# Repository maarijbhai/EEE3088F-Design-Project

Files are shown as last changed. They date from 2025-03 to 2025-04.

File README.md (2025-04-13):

# Micro Mouse Power Subsystem

This respository contains the datasheets of components used, schematics and production files of a power subsystem of a Micro Mouse. The power subsystem handles the charging, battery monitoring, motor controll and providing power to the various other subsections of a Micro Mouse.

## Table of Contents
- [Overview](#overview)
- [Subsytem Requirements](#subsystem-requirements)
- [File Structure](file-structure)
- [Usage](#usage)
- [Production](#production)
- [Credits](credits)

## Overview

Designed to navigate and solve a maze by itself, the Micro Mouse is a common project with even competitions made to determine who is able to create the fastest and most efficient Micro Mouse. While not on the competition level this project is undertaken by students in the University of Cape Town to put into practice all the theoretical knowledge learnt in their studies. With the hardware and sensoring subsystem designed by the university, the aim of this project is to design the power subsystem that powers the overall design.

## Subsystem Requirements

- Operate up to 4 motors bidirectionally with the pins available to you (listed in the power pinout table). You will need to control 2x brushed DC motors which could each draw 200mA at the highest voltage of a 1S1P battery (the battery is further specified in the battery section). The other 2x motors are for the auxiliary connection and need to operate 500mA each.
- Place an INA219 for monitoring the battery on the I2C Bus and configure it correctly with respect to the hardware (cannot have BOTH A0 AND A1 on GND)
- Charge the battery from the 9V input pin (listed in the power pinout table).
- Have two charging modes for a higher and lower charging current for the battery (200mA, and approximately 600mA ±100mA from the battery perspective.
- Integrate USB C and get 9V out of the USB Host
- Provide 2x External Load Switching at 1A each (High Side connected to your 5V)
- Provide a 3V3 5% accuracy (300mA max) and 5V Out 5% accuracy (1.5A max)
- Provide an ON/OFF switch. OFF state: battery draw <30uA. ON state: can provide your robot peak current of 2A. The switch needs to shut down 5V and 3V3.

## File Structure

Each of the above mentioned requirements are designed seperately under their own folder name ultimately meeting up in the Main project folder. This was to prevent any clashes or errors arising from outdated revisions of the project being worked on. 

The production files (gerbers) can be found inside the Main project folder under "JLCPCB".

## Usage

# Access schematic or PCB:
To view or modify the schematic and/or PCB:
1. Open KiCad 9 or later
2. Load the Main project (or any other desired)
3. Edit or simulate as needed

# To manufacture the PCB:
1. Navigate to the JLCPCB website
2. Upload the Gerber ZIP file
3. Use the provided BOM and CPL files in the JLCPCB file directory inside the main project folder for assembly

## Credits
- Maarij Alam
- Saeed Solomon

Third-party components from Texas Instruments, ON Semiconductor, and others.

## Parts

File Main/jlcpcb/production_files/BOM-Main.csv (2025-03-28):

Comment | Designator | Footprint | LCSC | Quantity
2.2u | C2,C5 | C_0402_1005Metric_Pad0.74x0.62mm_HandSolder | C12530 | 2
0.1u | C14 | C_0603_1608Metric_Pad1.08x0.95mm_HandSolder | C14663 | 1
10u | C18,C4 | C_0402_1005Metric_Pad0.74x0.62mm_HandSolder | C15525 | 2
0.01u | C3,C6 | C_0805_2012Metric_Pad1.18x1.45mm_HandSolder | C1710 | 2
10k | R19,R4 | R_0402_1005Metric_Pad0.72x0.64mm_HandSolder | C17414 | 2
150R | R12 | R_0815_2038Metric_Pad1.20x4.05mm_HandSolder | C17471 | 1
1R | R3 | R_1206_3216Metric_Pad1.30x1.75mm_HandSolder | C17928 | 1
1u | C1,C10,C11,C8 | C_1206_3216Metric_Pad1.33x1.80mm_HandSolder | C1848 | 4
10uF | C17,C19 | C_0402_1005Metric_Pad0.74x0.62mm_HandSolder | C19702 | 2
HUSB237-AA001-DN06R | U3 | DFN-6-1EP_2x2mm_P0.65mm_EP1.01x1.7mm | C22373734 | 1
330k | R20 | R_0603_1608Metric_Pad0.98x0.95mm_HandSolder | C23137 | 1
470k | R22 | R_0603_1608Metric_Pad0.98x0.95mm_HandSolder | C23178 | 1
75k | R1 | R_0603_1608Metric_Pad0.98x0.95mm_HandSolder | C23242 | 1
4.7u | C7,C9 | C_0402_1005Metric | C23733 | 2
R400 | R17,R5,R6 | R_1206_3216Metric_Pad1.30x1.75mm_HandSolder | C247521 | 3
RT9742GGJ5 | U4,U5 | TSOT-23-5_HandSoldering | C250547 | 2
100k | R18,R21 | R_0402_1005Metric_Pad0.72x0.64mm_HandSolder | C25741 | 2
10K | R14,R23 | R_0402_1005Metric_Pad0.72x0.64mm_HandSolder | C25744 | 2
1k5 | R7,R8 | R_0402_1005Metric_Pad0.72x0.64mm_HandSolder | C25867 | 2
2k2 | R11 | R_0402_1005Metric_Pad0.72x0.64mm_HandSolder | C25879 | 1
4k3 | R10 | R_0402_1005Metric_Pad0.72x0.64mm_HandSolder | C25899 | 1
TPS63802DLAR | U7 | VREG_TPS63802DLAR | C2845237 | 1
2k | R9 | R_0402_1005Metric_Pad0.72x0.64mm_HandSolder | C4109 | 1
22u | C12,C13 | C_0402_1005Metric_Pad0.74x0.62mm_HandSolder | C45783 | 2
BQ24074RGT | U1 | VQFN-16-1EP_3x3mm_P0.5mm_EP1.6x1.6mm | C54313 | 1
AMS1117-3.3 | U9 | SOT-223-3_TabPin2 | C6186 | 1
TYPE-C 6P | J2 | USB_C_Receptacle_GCT_USB4125-xx-x_6P_TopMnt_Horizontal | C668623 | 1
S9013 J3(RANGE:200-350) | Q3 | SOT-23_Handsoldering | C6749 | 1
INA219AxDCN | U6 | SOT-23-8_Handsoldering | C87469 | 1
47u | C15,C16 | C_0402_1005Metric_Pad0.74x0.62mm_HandSolder | C96123 | 2
DRV8833PW | U2 | TSSOP-16_4.4x5mm_P0.65mm |  | 1
TestPoint | TP18 | TestPoint_Pad_D1.0mm |  | 1
TestPoint | TP11 | TestPoint_Pad_D1.0mm |  | 1
TestPoint | TP4 | TestPoint_Pad_D1.0mm |  | 1
DRV8833PW | U8 | TSSOP-16_4.4x5mm_P0.65mm |  | 1
1k | R13 | R_0402_1005Metric_Pad0.72x0.64mm_HandSolder |  | 1
TestPoint | TP14 | TestPoint_Pad_D1.0mm |  | 1
TestPoint | TP13 | TestPoint_Pad_D1.0mm |  | 1
TestPoint | TP2 | TestPoint_Pad_D1.0mm |  | 1
KT-0603R | D1 | LED_KT-0603R |  | 1
TestPoint | TP6 | TestPoint_Pad_D1.0mm |  | 1
TestPoint | TP15 | TestPoint_Pad_D1.0mm |  | 1
TestPoint | TP9 | TestPoint_Pad_D1.0mm |  | 1
TestPoint | TP12 | TestPoint_Pad_D1.0mm |  | 1
TestPoint | TP16 | TestPoint_Pad_D1.0mm |  | 1
TestPoint | TP8 | TestPoint_Pad_D1.0mm |  | 1
KT-0603R | D2 | LED_KT-0603R |  | 1
TestPoint | TP17 | TestPoint_Pad_D1.0mm |  | 1
TestPoint | TP3 | TestPoint_Pad_D1.0mm |  | 1
TestPoint | TP19 | TestPoint_Pad_D1.0mm |  | 1
TestPoint | TP5 | TestPoint_Pad_D1.0mm |  | 1
TestPoint | TP10 | TestPoint_Pad_D1.0mm |  | 1
SS-12D11G3R | SW2 | SW-TH_SS-12D11L3 |  | 1
TestPoint | TP1 | TestPoint_Pad_D1.0mm |  | 1
470nH | L1 | L_0603_1608Metric_Pad1.05x0.95mm_HandSolder |  | 1
TestPoint | TP7 | TestPoint_Pad_D1.0mm |  | 1
TestPoint | TP20 | TestPoint_Pad_D1.0mm |  | 1

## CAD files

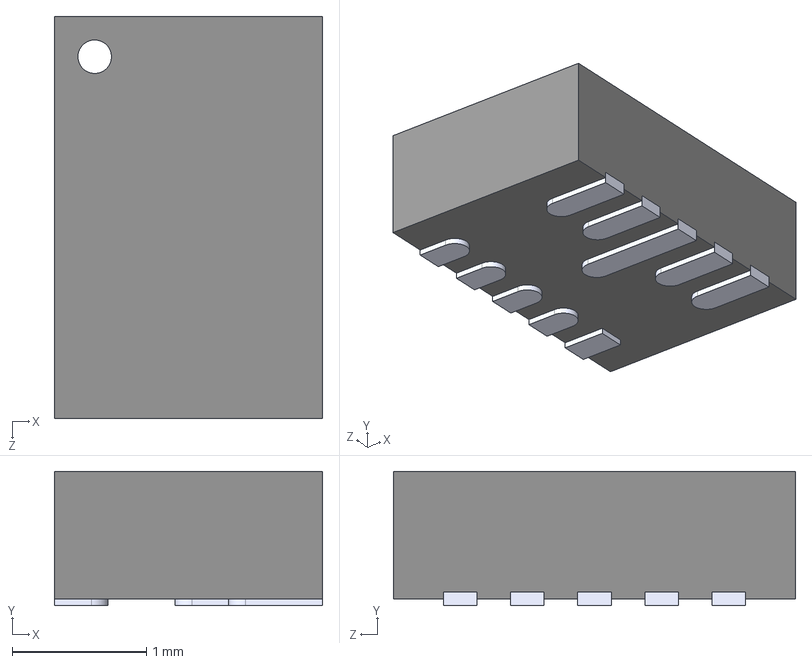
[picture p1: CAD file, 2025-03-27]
Component Footprints/TPS63802DLAR/TPS63802DLAR.step
2.00 x 1.00 x 3.00 mm

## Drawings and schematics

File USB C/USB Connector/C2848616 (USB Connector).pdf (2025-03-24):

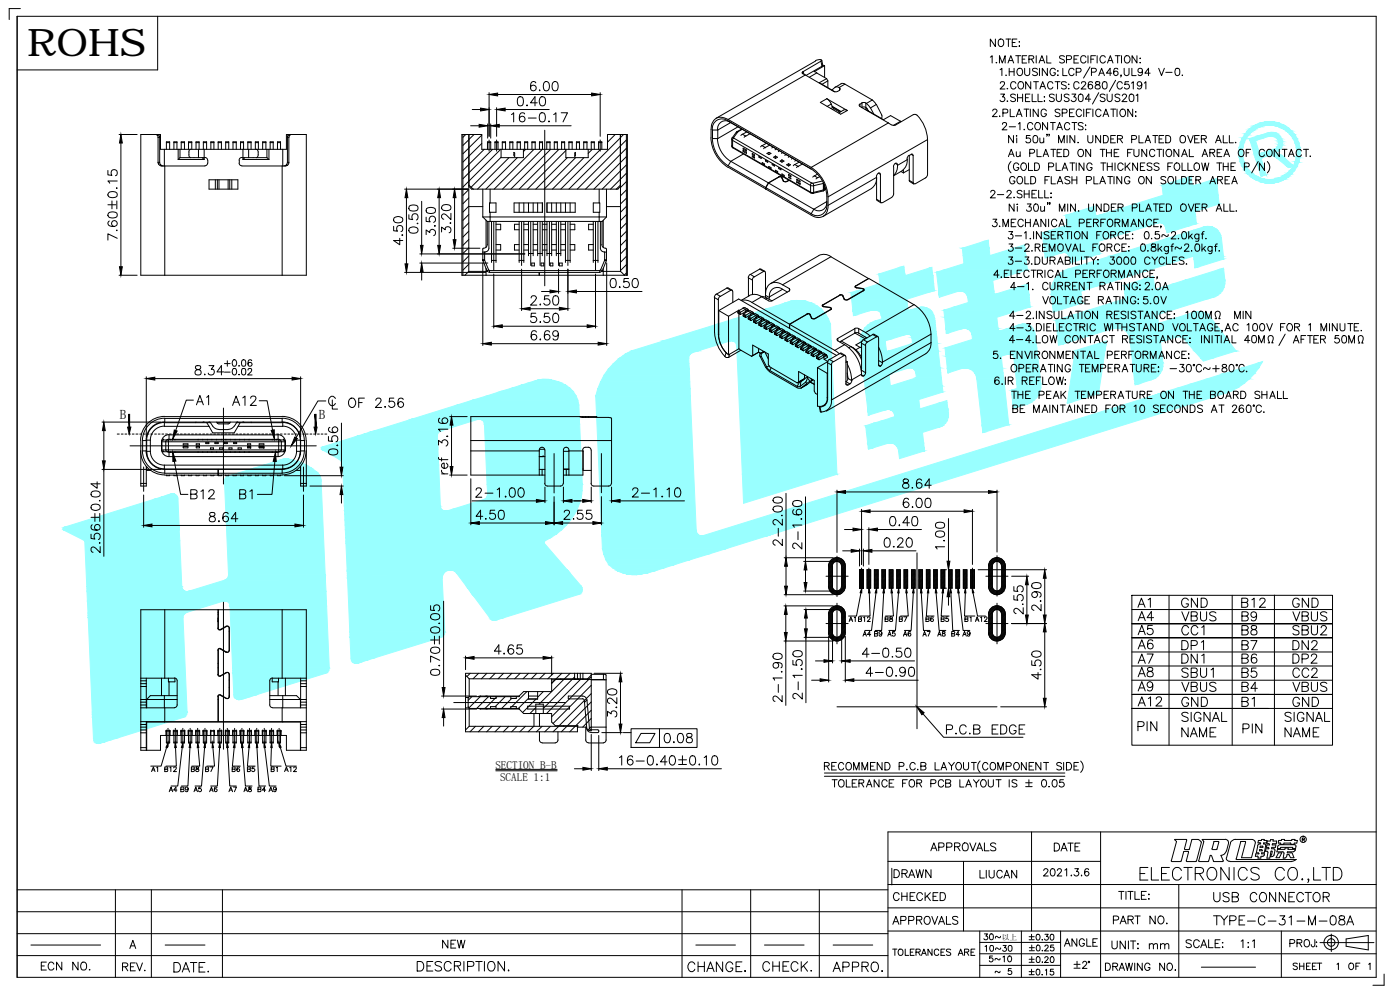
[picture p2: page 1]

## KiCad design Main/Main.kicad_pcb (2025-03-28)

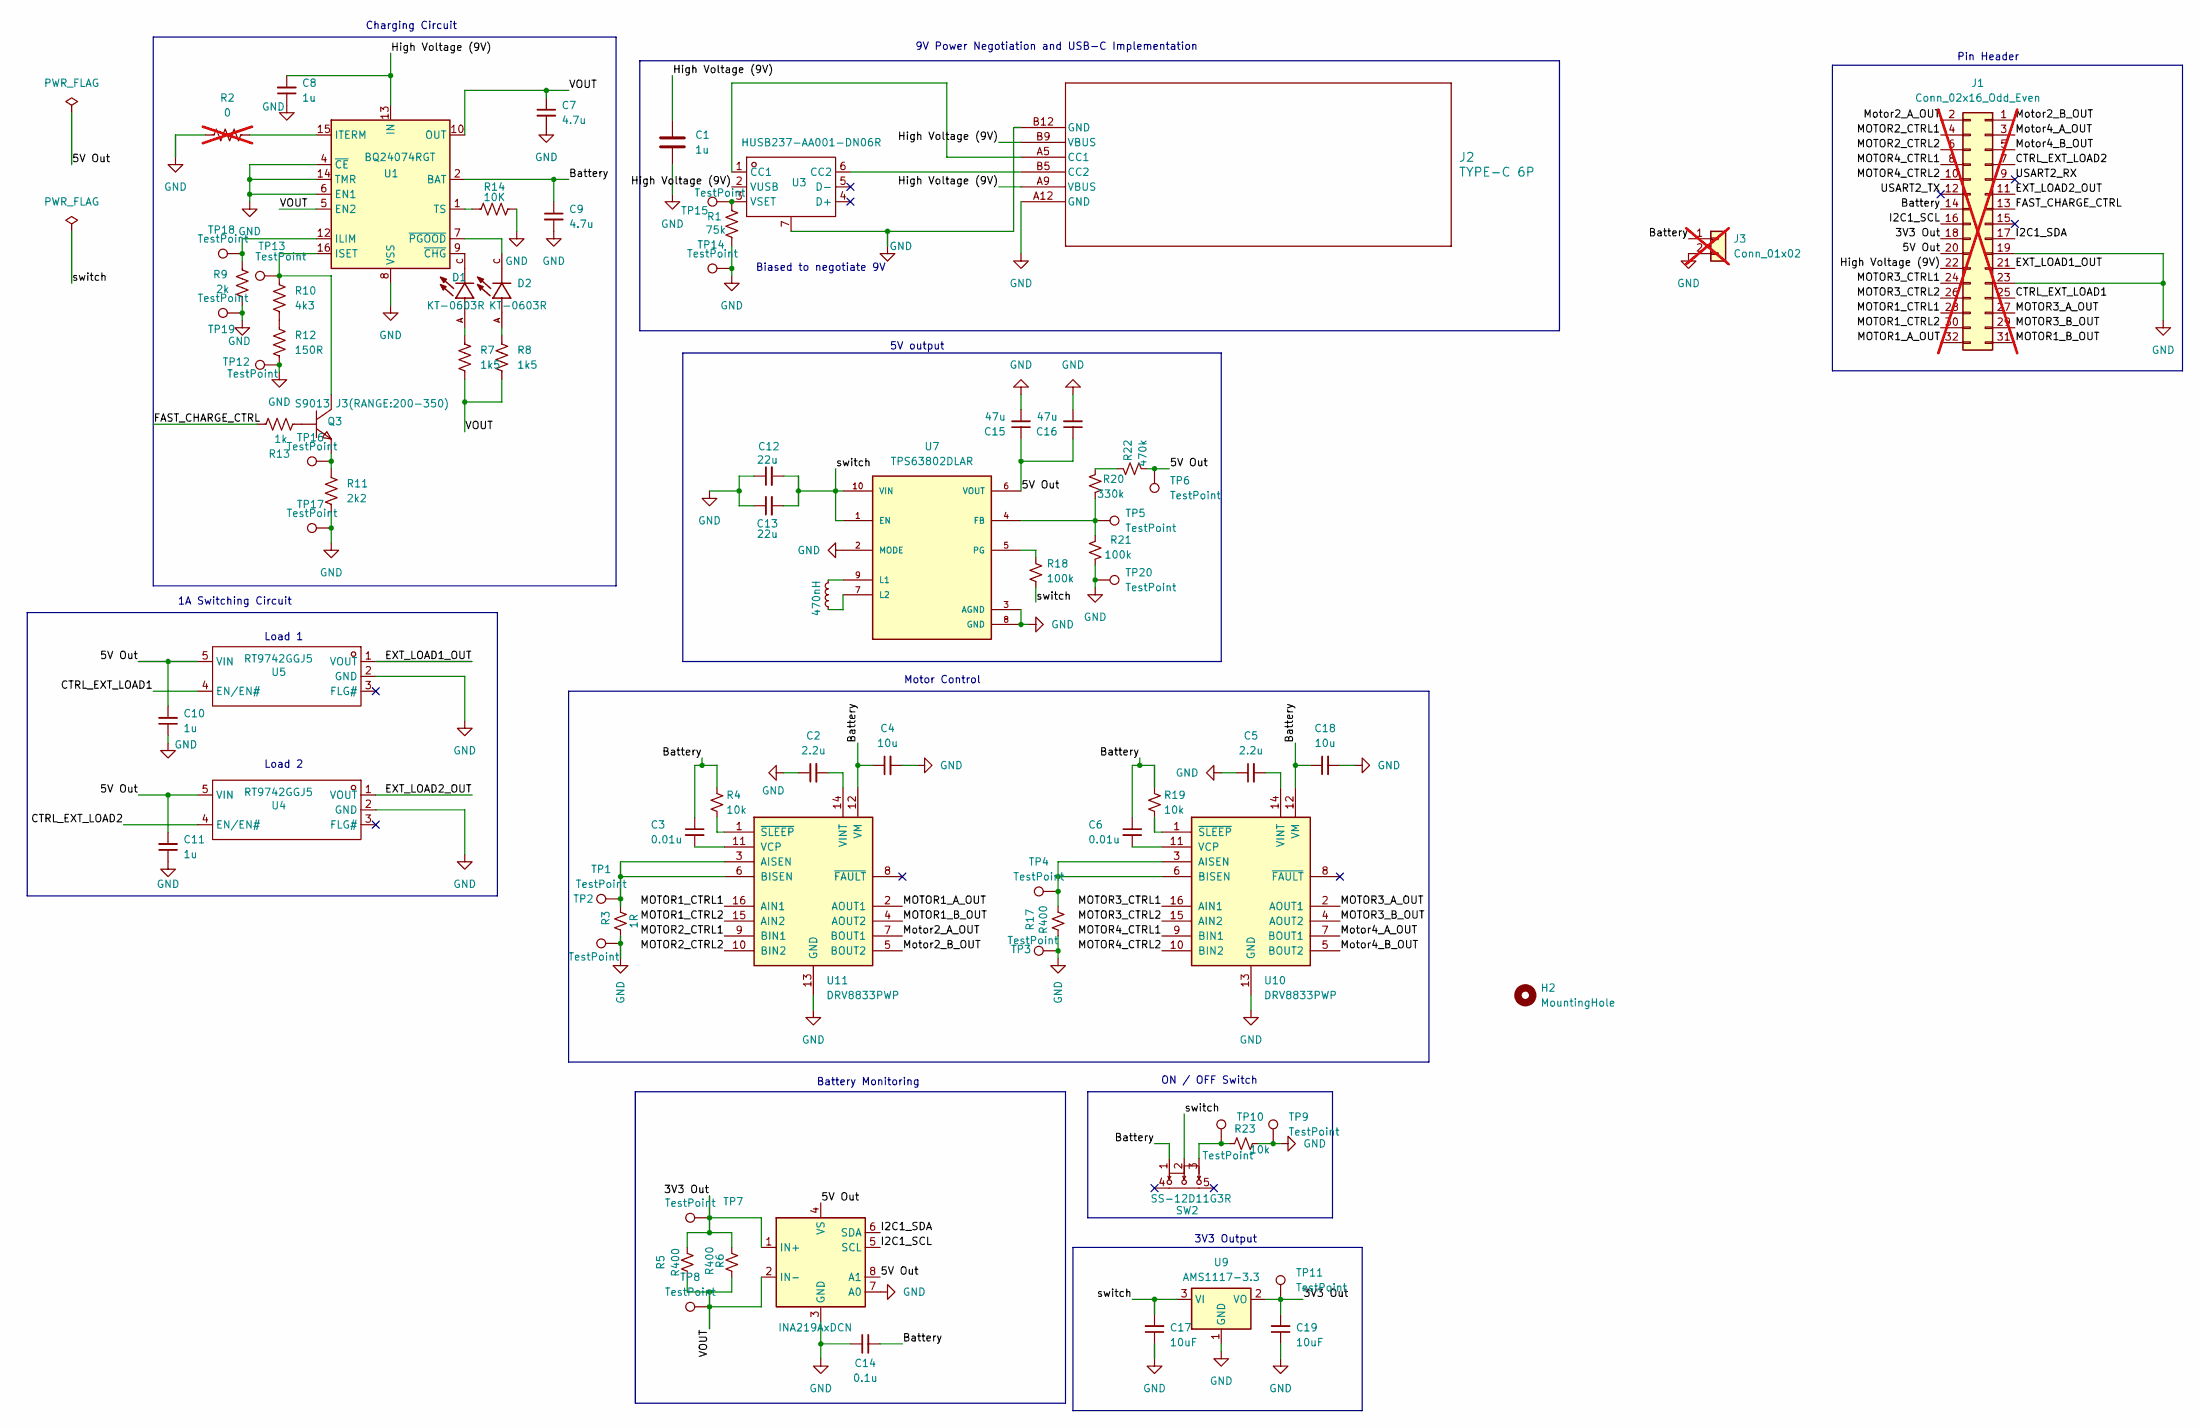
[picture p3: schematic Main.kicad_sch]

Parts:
C1, C8, C10, C11: 1u; C_1206_3216Metric_Pad1.33x1.80mm_HandSolder; LCSC C1848
C2, C5: 2.2u; C_0402_1005Metric_Pad0.74x0.62mm_HandSolder; LCSC C12530
C3, C6: 0.01u; C_0805_2012Metric_Pad1.18x1.45mm_HandSolder; LCSC C1710
C4, C18: 10u; C_0402_1005Metric_Pad0.74x0.62mm_HandSolder; LCSC C15525
C7: 4.7u; C_0402_1005Metric; LCSC C23733
C9: 4.7u; C_0402_1005Metric_Pad0.74x0.62mm_HandSolder; LCSC C23733
C12, C13: 22u; C_0402_1005Metric_Pad0.74x0.62mm_HandSolder; LCSC C45783
C14: 0.1u; C_0603_1608Metric_Pad1.08x0.95mm_HandSolder; LCSC C14663
C15, C16: 47u; C_0402_1005Metric_Pad0.74x0.62mm_HandSolder; LCSC C96123
C17, C19: 10uF; C_0402_1005Metric_Pad0.74x0.62mm_HandSolder; LCSC C19702
D1, D2: KT-0603R; LED_KT-0603R; PARTREV 2013/01/24
H2: MountingHole; MountingHole_3.2mm_M3
J1: Conn_02x16_Odd_Even; PinHeader_2x16_P2.54mm_Vertical; not fitted
J2: TYPE-C 6P; USB_C_Receptacle_GCT_USB4125-xx-x_6P_TopMnt_Horizontal; LCSC C668623
J3: Conn_01x02; JST_PH_S2B-PH-K_1x02_P2.00mm_Horizontal; not fitted
L1: 470nH; L_0603_1608Metric_Pad1.05x0.95mm_HandSolder
Q3: S9013 J3(RANGE:200-350); SOT-23_Handsoldering; MANUFACTURER PART S9013 J3(RANGE:200-350); LCSC PART NAME NPN 电流:500mA 耐压:25V H档(200-350)
R1: 75k; R_0603_1608Metric_Pad0.98x0.95mm_HandSolder; LCSC C23242
R2: 0; R_0402_1005Metric_Pad0.72x0.64mm_HandSolder; not fitted
R3: 1R; R_1206_3216Metric_Pad1.30x1.75mm_HandSolder; LCSC C17928
R4, R19: 10k; R_0402_1005Metric_Pad0.72x0.64mm_HandSolder; LCSC C17414
R5, R6, R17: R400; R_1206_3216Metric_Pad1.30x1.75mm_HandSolder; LCSC C247521
R7, R8: 1k5; R_0402_1005Metric_Pad0.72x0.64mm_HandSolder; LCSC C25867
R9: 2k; R_0402_1005Metric_Pad0.72x0.64mm_HandSolder; LCSC C4109
R10: 4k3; R_0402_1005Metric_Pad0.72x0.64mm_HandSolder; LCSC C25899
R11: 2k2; R_0402_1005Metric_Pad0.72x0.64mm_HandSolder; LCSC C25879
R12: 150R; R_0815_2038Metric_Pad1.20x4.05mm_HandSolder; LCSC C17471
R13: 1k; R_0402_1005Metric_Pad0.72x0.64mm_HandSolder
R14: 10K; R_0402_1005Metric_Pad0.72x0.64mm_HandSolder; LCSC C25744
R18, R21: 100k; R_0402_1005Metric_Pad0.72x0.64mm_HandSolder; LCSC C25741
R20: 330k; R_0603_1608Metric_Pad0.98x0.95mm_HandSolder; LCSC C23137
R22: 470k; R_0603_1608Metric_Pad0.98x0.95mm_HandSolder; LCSC C23178
R23: 10k; R_0402_1005Metric_Pad0.72x0.64mm_HandSolder; LCSC C25744
SW2: SS-12D11G3R; SW-TH_SS-12D11L3; CURRENT RATING (DC) 3A; VOLTAGE RATING (DC) 125V; MANUFACTURER PART SS-12D11G3R; LCSC PART NAME 柄长3mm 弯插双档 滑动开关
TP1, TP2, TP3, TP4, TP5, TP6, TP7, TP8, TP9, TP10, TP11, TP12, TP13, TP14, TP15, TP16, TP17, TP18, TP19, TP20: TestPoint; TestPoint_Pad_D1.0mm
U1: BQ24074RGT; VQFN-16-1EP_3x3mm_P0.5mm_EP1.6x1.6mm; LCSC C54313
U3: HUSB237-AA001-DN06R; DFN-6-1EP_2x2mm_P0.65mm_EP1.01x1.7mm; MANUFACTURER PART HUSB237-AA001-DN06R; LCSC PART NAME HUSB237-AA001-DN06R
U4, U5: RT9742GGJ5; TSOT-23-5_HandSoldering; INPUT VOLTAGE 2.7V~6V; MANUFACTURER PART RT9742GGJ5; LCSC PART NAME RT9742GGJ5
U6: INA219AxDCN; SOT-23-8_Handsoldering; LCSC C87469
U7: TPS63802DLAR; VREG_TPS63802DLAR; PARTREV B; DigiKey_Part_Number 296-TPS63802DLARTR-ND
U9: AMS1117-3.3; SOT-223-3_TabPin2; LCSC C6186
U10, U11: DRV8833PWP; HTSSOP-16-1EP_4.4x5mm_P0.65mm_EP3.4x5mm_Mask2.46x2.31mm; LCSC C1556089

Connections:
/3V3 Out: C19.2, J1.18, R5.2, R6.2, TP7.1, TP11.1, U6.1 (IN+), U9.2 (VO)
/5V Out: C10.2, C11.2, C15.1, C16.1, J1.20, R22.2, TP6.1, U4.5 (VIN), U5.5 (VIN), U6.4 (VS), U6.8 (A1), U7.6 (VOUT)
/Battery: C3.1, C4.1, C6.1, C9.1, C14.2, C18.1, J1.14, J3.1, R4.1, R19.1, SW2.1, U1.2 (BAT), U1.3 (BAT), U10.12 (VM), U11.12 (VM)
/CTRL_EXT_LOAD1: J1.25, U5.4 (EN/EN#)
/CTRL_EXT_LOAD2: J1.7, U4.4 (EN/EN#)
/EXT_LOAD1_OUT: J1.21, U5.1 (VOUT)
/EXT_LOAD2_OUT: J1.11, U4.1 (VOUT)
/FAST_CHARGE_CTRL: J1.13, R13.1
/High Voltage (9V): C1.1, C8.2, J1.22, J2.A9 (VBUS), J2.B9 (VBUS), U1.13 (IN), U3.2 (VUSB)
/I2C1_SCL: J1.16, U6.5 (SCL)
/I2C1_SDA: J1.17, U6.6 (SDA)
/MOTOR1_A_OUT: J1.32, U11.2 (AOUT1)
/MOTOR1_B_OUT: J1.31, U11.4 (AOUT2)
/MOTOR1_CTRL1: J1.28, U11.16 (AIN1)
/MOTOR1_CTRL2: J1.30, U11.15 (AIN2)
/MOTOR2_CTRL1: J1.4, U11.9 (BIN1)
/MOTOR2_CTRL2: J1.6, U11.10 (BIN2)
/MOTOR3_A_OUT: J1.27, U10.2 (AOUT1)
/MOTOR3_B_OUT: J1.29, U10.4 (AOUT2)
/MOTOR3_CTRL1: J1.24, U10.16 (AIN1)
/MOTOR3_CTRL2: J1.26, U10.15 (AIN2)
/MOTOR4_CTRL1: J1.8, U10.9 (BIN1)
/MOTOR4_CTRL2: J1.10, U10.10 (BIN2)
/Motor2_A_OUT: J1.2, U11.7 (BOUT1)
/Motor2_B_OUT: J1.1, U11.5 (BOUT2)
/Motor4_A_OUT: J1.3, U10.7 (BOUT1)
/Motor4_B_OUT: J1.5, U10.5 (BOUT2)
/USART2_RX: J1.9
/USART2_TX: J1.12
/VOUT: C7.1, R5.1, R6.1, R7.2, R8.2, TP8.1, U1.5 (EN2), U1.10 (OUT), U1.11 (OUT), U6.2 (IN-)
/switch: C12.2, C13.2, C17.2, R18.2, SW2.2, U7.1 (EN), U7.10 (VIN), U9.3 (VI)
GND: C1.2, C2.1, C4.2, C5.1, C7.2, C8.1, C9.2, C10.1, C11.1, C12.1, C13.1, C14.1, C15.2, C16.2, C17.1, C18.2, C19.1, J1.19, J1.23, J2.A12 (GND), J2.B12 (GND), J3.2, R1.2, R2.1, R3.1, R9.2, R11.2, R12.2, R14.2, R17.1, R21.2, R23.1, TP2.1, TP3.1, TP9.1, TP12.1, TP14.1, TP17.1, TP19.1, TP20.1, U1.4 (~CE), U1.6 (EN1), U1.8 (VSS), U1.14 (TMR), U1.17 (VSS), U3.7 (GND), U4.2 (GND), U5.2 (GND), U6.3 (GND), U6.7 (A0), U7.2 (MODE), U7.3 (AGND), U7.8 (GND), U9.1 (GND), U10.13 (GND), U10.17 (GND), U11.13 (GND), U11.17 (GND)
unnamed: D1.A, R7.1
unnamed: D2.A, R8.1
unnamed: J2.A5 (CC1), U3.1 (CC1)
unnamed: J2.B5 (CC2), U3.6 (CC2)
unnamed: Q3.1 (B), R13.2
unnamed: Q3.3 (C), R10.1, TP13.1, U1.16 (ISET)
unnamed: Q3.2 (E), R11.1, TP16.1
unnamed: R10.2, R12.1
unnamed: R20.1, R22.1
unnamed: R23.2, SW2.3, TP10.1
unnamed: R9.1, TP18.1, U1.12 (ILIM)
unnamed: R2.2, U1.15 (ITERM)
unnamed: R14.1, U1.1 (TS)
unnamed: D1.C, U1.9 (~CHG)
unnamed: D2.C, U1.7 (~PGOOD)
unnamed: R1.1, TP15.1, U3.3 (VSET)
unnamed: R20.2, R21.1, TP5.1, U7.4 (FB)
unnamed: L1.2, U7.9 (L1)
unnamed: L1.1, U7.7 (L2)
unnamed: R18.1, U7.5 (PG)
unnamed: R17.2, TP4.1, U10.3 (AISEN), U10.6 (BISEN)
unnamed: C6.2, U10.11 (VCP)
unnamed: C5.2, U10.14 (VINT)
unnamed: R19.2, U10.1 (~SLEEP)
unnamed: R3.2, TP1.1, U11.3 (AISEN), U11.6 (BISEN)
unnamed: C3.2, U11.11 (VCP)
unnamed: C2.2, U11.14 (VINT)
unnamed: R4.2, U11.1 (~SLEEP)

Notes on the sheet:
ON / OFF Switch
1A Switching Circuit
Battery Monitoring
Pin Header
9V Power Negotiation and USB-C Implementation
Charging Circuit
5V output
3V3 Output
Motor Control
Biased to negotiate 9V
Load 2
Load 1

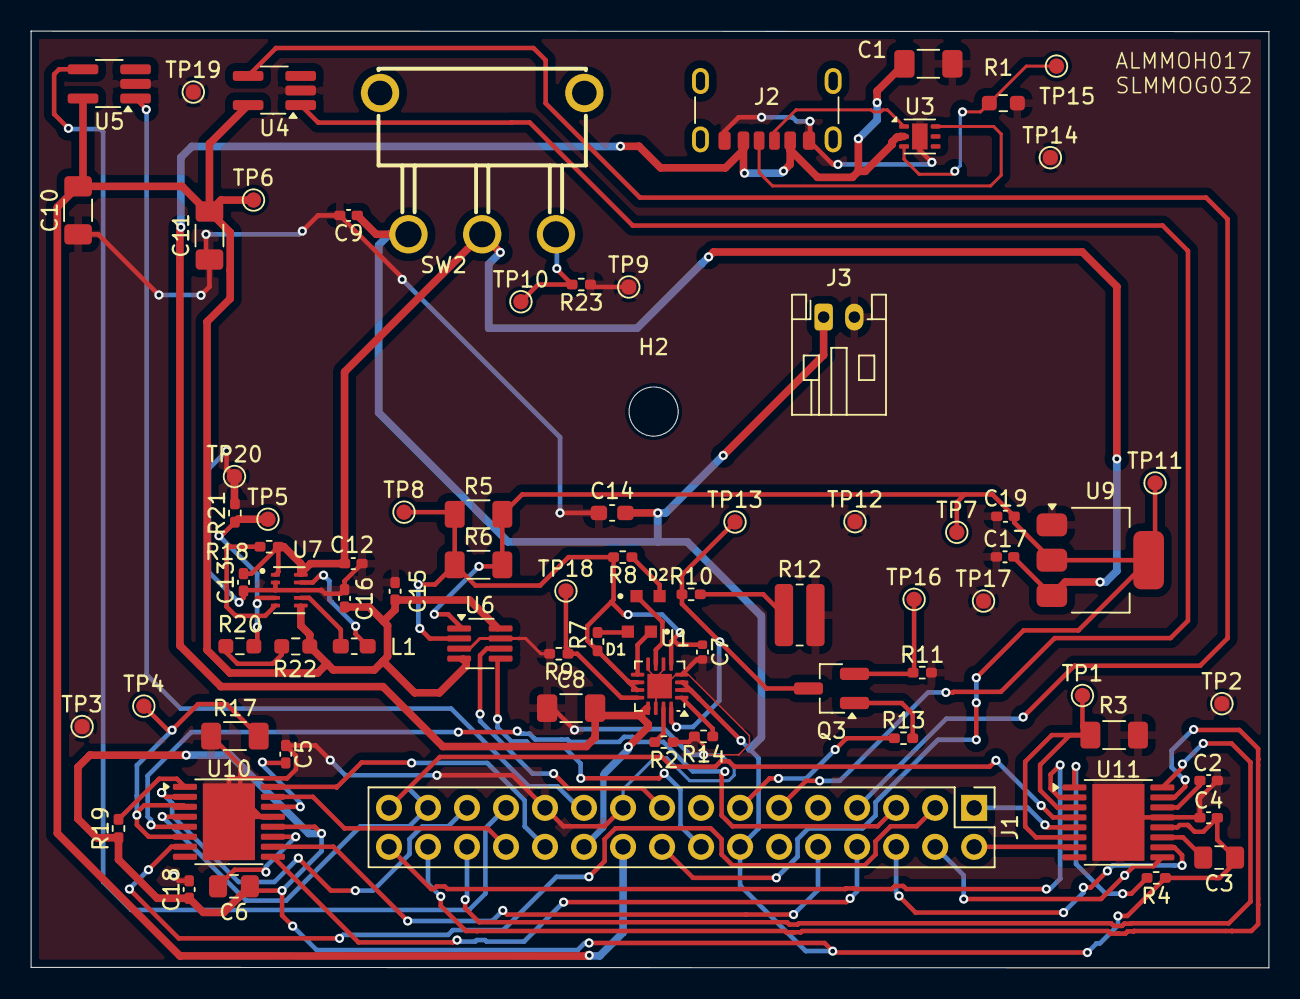
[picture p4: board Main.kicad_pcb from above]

Board: 2 copper layers, 80.6 x 61.0 mm, 78 parts (0 on the bottom side), 58 nets.

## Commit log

2025-03-21 INA219 configuration
    Added a KiCad project to set up and configure the INA219. Datasheet attached as well.
    [INA219 Monitoring.kicad_pcb, INA219 Monitoring.kicad_sch]
2025-03-23 Started 3V3 and 5V out
    Started working in the 3V3 and 5V output module and assigned footprints to the INA219 module
    [3V3 and 5V.kicad_pcb, 3V3 and 5V.kicad_sch, INA219 Monitoring.kicad_sch]
2025-03-24 USB C Integration KiCad
    [USB C_Power and Integration.kicad_pcb, USB C_Power and Integration.kicad_sch, temp.kicad_pcb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]
2025-03-24 Added bidirectional motor control section
    Completed the bidirectional motor control part of the system as well as finished the remaining part of the 3V3 and 5V out.
    [3V3 and 5V.kicad_sch, INA219 Monitoring.kicad_sch, Motor Control.kicad_pcb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]
2025-03-25 All MJ's requirements schematics done (review pending)
    [USB C_Power and Integration.kicad_sch]
2025-03-26 ON/OFF switch
    Completed the ON/OFF switch.
    [3V3 and 5V.kicad_sch, Comined_S.kicad_pcb, Comined_S.kicad_sch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]
2025-03-26 Changed switch
    Changed switch do not depend on p-mosfet
    [Comined_S.kicad_sch, temp.kicad_sch]
2025-03-26 Polished USB C Power and Charging Integration and Switching Circuit with Footprints
    [USB C_Power and Integration.kicad_sch]
2025-03-26 Made it look more professional
    [Comined_S.kicad_sch]
2025-03-26 Created the Main File combining our schematics
    [Main.kicad_pcb, Main.kicad_sch]
2025-03-26 Some few fixes on pin assignments
    [Main.kicad_sch]
2025-03-27 Added footprints
    Added footprints for a few missing ICs
    [SS-12D11G3R1_SS-12D11G3R.schdoc, TPS63802DLAR.step]
2025-03-27 Changed pins
    [Main.kicad_sch]
2025-03-27 added other footprints
    [SS-12D11G3R1_SS-12D11G3R.schdoc, SW-TH_SS-12D11G5R_2025-03-26.pcbdoc, TPS63802DLAR.step]
2025-03-27 Changed Some Pin Names
    [Main.kicad_sch]
2025-03-27 Made some pin label changes
    [Main.kicad_sch]
2025-03-27 push before pcb
    [Main.kicad_pcb]
2025-03-27 Started PCB and Started Adding test points
    [Main.kicad_pcb, Main.kicad_sch]
2025-03-27 Got ALL the footprints present
    [Main.kicad_sch]
2025-03-27 connected first motor control
    [Main.kicad_pcb]
2025-03-27 Did some error fixing
    [Main.csv, Main.kicad_sch]
2025-03-27 Corrected LCSC of parts
    Initially accidentally labelled the LCSC of components as (LSCS) which generated an error. This version fixed these issues.
    [Main.kicad_sch]
2025-03-27 Changed maximum motor voltage
    [Main.kicad_sch]
2025-03-28 Completed substantial PCB Connections
    Completed: 1A Switching, Charging IC
    [Main.csv, Main.kicad_pcb, Main.kicad_sch]
2025-03-28 Finished 9V implementation and PD system
    [Main.kicad_pcb]
2025-03-28 Added the Switch and Connected the Battery pin to it
    [Main.kicad_pcb]
2025-03-28 Removed the GND for one of the motor ICs
    Pouring ground so ground not connected
    [Main.kicad_pcb]
2025-03-28 PB-13 was unconnected - it is now connected
    [Main.kicad_pcb, Main.kicad_sch]
2025-03-28 Changed all my 9V wires to 0,5mm
    [Main.kicad_pcb]
2025-03-28 connected other motor
    [Main.kicad_pcb, Main.kicad_sch]
2025-03-28 Poured Ground and connected all PCB items
    [Main.csv, Main.kicad_pcb]
2025-03-28 Using a new Motor Driver bc old one no stock
    [BOM-Main.csv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]
2025-03-28 NO ERRORS
    [Main.kicad_pcb, Main.kicad_sch]
2025-04-13 Changed Folders
    Neatened up the repository by renaming folders and deleting any unnecessary items.
    [Comined_S.kicad_pcb, Comined_S.kicad_sch, SS-12D11G3R1_SS-12D11G3R.schdoc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]
